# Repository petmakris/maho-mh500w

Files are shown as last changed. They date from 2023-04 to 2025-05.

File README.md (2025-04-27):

# Maho MH500w CNC

Documentation and notes for a Maho MH500W CNC

## Selecting Heidenhain EXE (converters for 

LS-403C has a grating period of 20μm ==> 1 μm resolution in 5 fold interpolation

# Linux CNC Installation

# Software Installation

Start of `bookworm/sid` (use xfce):

https://cdimage.debian.org/cdimage/unofficial/non-free/cd-including-firmware/

- Remove cdrom from sources: sudo nano /etc/sources.list
- `sudo apt install ethtool`

Check driver alignment:

- `lspci`
- `sudo ethtool -i enp2s0`

## Install Rods' custom kernel

6.1 exists in my NAS

- install headers
- install kernel
- `sudo apt install grub-customizer`
- `sudo apt install r8168-dkms`

# Mesa 7i97

## Network interface:

`sudo vim /etc/network/interfaces`

```
auto enp2s0
iface enp2s0 inet static
address 10.10.10.1 or 192.168.1.1
```
Restart network: `sudo systemctl restart networking`

`mesaflash --device 7i97 --addr 10.10.10.10 --readhmid`

# ??? sudo ethtool -C eth0 rx-usecs 0

# LinuxCNC

`sudo apt install linuxcnc-uspace linuxcnc-uspace-dev mesaflash`

Let it run for a while. While it is running,
in another window, check the network latency by reviewing the TMAX settings on your card

`halcmd show param hm2*tmax*`

```
Parameters:
Owner   Type  Dir         Value  Name
     7  s32   RW              0  hm2_7i97.0.read-request.tmax
     7  bit   RO          FALSE  hm2_7i97.0.read-request.tmax-increased
     7  s32   RW         704022  hm2_7i97.0.read.tmax
     7  bit   RO          FALSE  hm2_7i97.0.read.tmax-increased
     7  s32   RW          42126  hm2_7i97.0.write.tmax
     7  bit   RO          FALSE  hm2_7i97.0.write.tmax-increased
```

# Notes

[Enable outputs](https://forum.linuxcnc.org/27-driver-boards/46253-mesa-7i97-analog-out-issue#246257)

# Notes

- MAHO Original color: RAL6011

## Pull Stud

- SK40 ISO 7388 II B
  - The short pull stud for SK
  - The long for BT 



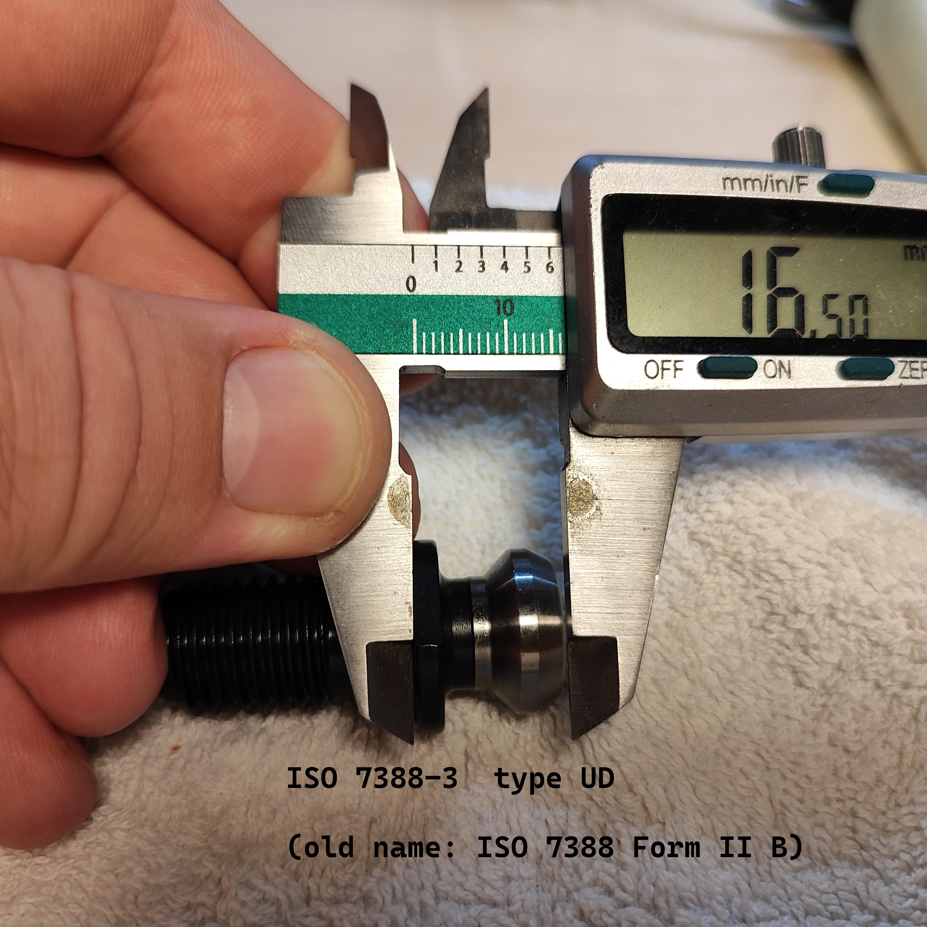
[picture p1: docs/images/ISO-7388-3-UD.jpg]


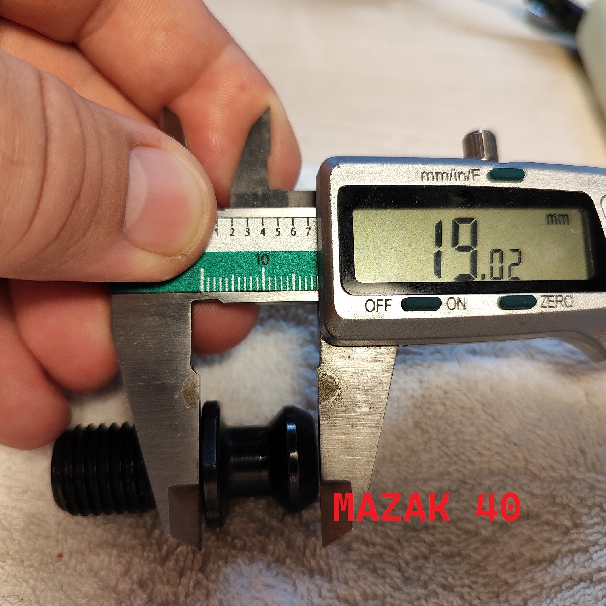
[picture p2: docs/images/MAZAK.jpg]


ISO Standard: https://www.iso.org/standard/68845.html

What fits to a CAT40 cone:
    Pull studs ISO 7388-3 Form UD | M16 | former norm ISO 7388 Form II B (https://bit.ly/38K9Pz4)
    Kemmler
        Order number: 404.20.16
        https://www.kemmler-shop.de/en/pull-studs/pull-studs-iso-7388/1509/pull-studs-iso-7388-3-form-ud-m16-with-drill-through-without-o-ring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

What fits to a BT40 cone:
    Longer by 3mm.
    Kemmler:
        Order number: 404.20.16.20
        https://www.kemmler-shop.de/en/pull-studs/pull-studs-iso-7388/1511/pull-studs-iso-7388-3-form-ud-m16-with-drill-through-incl.-o-ring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

# Gallery









received (1)

received (6)

received (7)

received (9)

received (50)

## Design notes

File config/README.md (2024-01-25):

# Limits

LJ12A3-4-Z/EX - Output Type: NPN NO (Normal Open)

```
Axis    Desc        Cable       Exten.      Name        MESA 7i97
----------------------------------------------------------------------
        Vcc         Brown       Brown       lim-x-pwr   24V
Χ       Signal      Black       White       lim-x-out   TB4-pin4-IN2
        Ground      Blue        Green       lim-x-com   TB4-pin6-COMMON-2,3

        Vcc         Brown       Brown       lim-y-pwr   24V
Y       Signal      Black       White       lim-y-out   TB4-pin5-IN3
        Ground      Blue        Green       lim-y-com   TB4-pin6-COMMON-2,3

        Vcc         Brown       Brown       lim-z-pwr   24V 
Z       Signal      Black       White       lim-z-out   TB4-pin7-IN4
        Ground      Blue        Green       lim-z-com   TB4-pin9-COMMON-4,5
```

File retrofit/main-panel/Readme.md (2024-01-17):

# Requirements

Out of 32 inputs use

- Use a potentiometer for jogging      POT2218PS2-10K 
- Use a potentiometer for Feed Over    POT2218PS2-10K 
- Use a potentiometer for Spindle      POT2218PS2-10K 

- 4 for analog
- 6 for pendant
- 18 for generic buttons

==> Out of 16 output, 12 to be used by LEDs

LED green   6x TME 19010351
LED red     6x TME 19010353

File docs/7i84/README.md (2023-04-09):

The Smart Serial Card Configuration is very new.

At this time the Smart Serial Card will create
a net with a signal name and you will have to 
add the input or output pin name or create simple 
I/O connections.

The 7i83 and 7i87 are not currently supported.

The Smart Serial Card configuration will not load
from the ini file at this time.

## SSERIAL Wiring using a standard CAT5 Cable:

Pin 0 is at the bottom

TB2 PIN	    SIGNAL      CAT5 PIN	CAT5 568B COLOR
--------------------------------------------------------
15	        GND	        4,5	        BLUE, BLUE / WHITE
16	        RX+	        6	        GREEN
17	        RX-	        3	        GREEN / WHITE
18	        TX+	        2	        ORANGE
19	        TX-	        1	        ORANGE / WHITE
20	        +5V	        7,8	        BROWN / WHITE,BROWN

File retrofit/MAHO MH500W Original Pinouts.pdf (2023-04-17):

19X7 | Inputs | Color
19X7-1 | Handwheel X | ws | white | 278
19X7-2 | Handwheel Y | br | brown | 279
19X7-3 | Handwheel Z | gn | green | 280
19X7-4 | 24V (αυτο ειναι ένδειξη) | ge | yellow | 200
19X7-5 | Spindle OFF | gr | gray | 211
19X7-6 | / (Spindle Feed Stop) | rs | orange | 212
19X7-7 | Lubricant Pump Feedback | bl | blue | 213
19X7-8 | No Function | rt | red
19X7-34 | | sw | black
19X6 | Outputs | Color | | | Relay
19X6-1 | X Axis Handwheel Clutch | ws | white | 28A1-3 | 28A1-K2
19X6-2 | Y Axis Handwheel Clutch | br | brown | 28A1-4 | 28A1-K3
19X6-3 | Z Axis Handwheel Clutch | gn | green | 28A1-5 | 28A1-K4
19X6-4 | Spindle CW | ge | yellow | 28A1-14 | 28A1-K6
19X6-5 | Spindle CCW | gr | gray | 28A1-28 | 28A1-K7
19X6-6 | Coolant Pump | rs | orange | 28A1-29 | 28A1-K8
19X6-7 | Tool Release | bl | blue | 28A1-30 | 28A1-K9
19X6-8 | Central Lubrication | rt | red | 313 | 4V1 / 4K1
19X6-9 | No Function
19X6-34 | / ESTOP | sw | black | 28A1-2 | 28A1-K1
19X4 | Setpoint | Color
19X4-1 | X Axis | br | brown | E101
19X4-2 | X Axis | bl | blue | E102
19X4-3 | Y Axis | ws | white | E201
19X4-4 | Y Axis | gr | green | E202
19X4-5 | Z Axis | ge | yellow | E301
19X4-6
19X4-7
19X4-8
19X4-9 | Z Axis | rs | rs | E302
28A1 | Relay Board
K1 | Emergency Stop Switch
K2 | X Axis Handwheel Clutch
K3 | Y Axis Handwheel Clutch
K4 | Z Axis Handwheel Clutch
K5
K6 | Main Drive Anti-Clockwise
K7 | Main Drive Left Rotation
K8 | Release Tool Clump
K9 | Lubricant Pump
K10

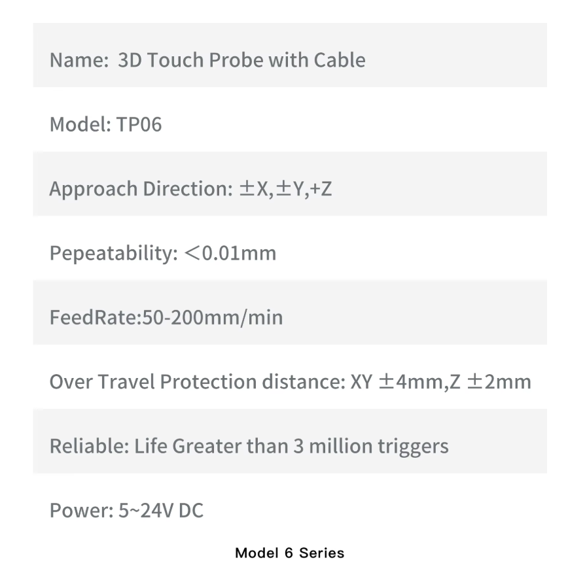
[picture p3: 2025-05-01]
docs/Probe/aliexpress-probe/specs.png

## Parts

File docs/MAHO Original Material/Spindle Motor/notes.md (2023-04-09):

ABGA-090LB-04A 

Page 90 in PDF (Brake morots, Series ABGA)

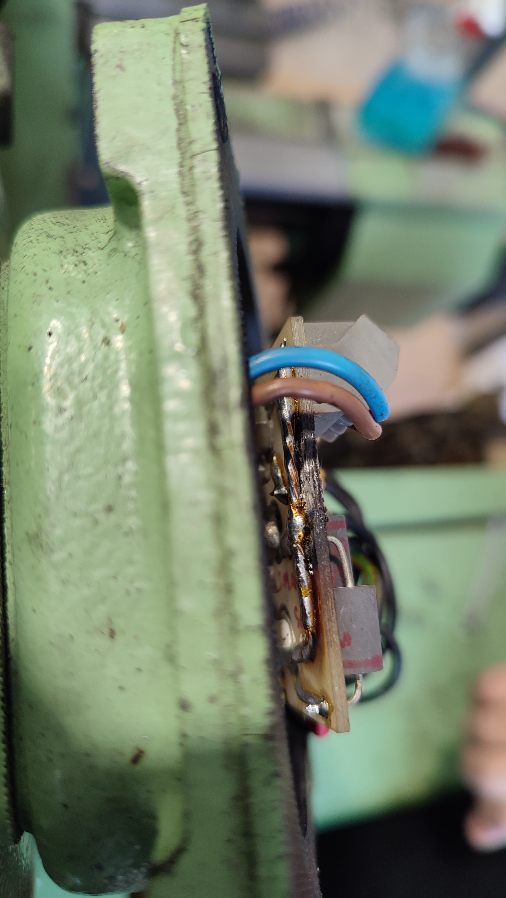
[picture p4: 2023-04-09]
docs/MAHO Original Material/Spindle Motor/gallery/junction-7.jpg

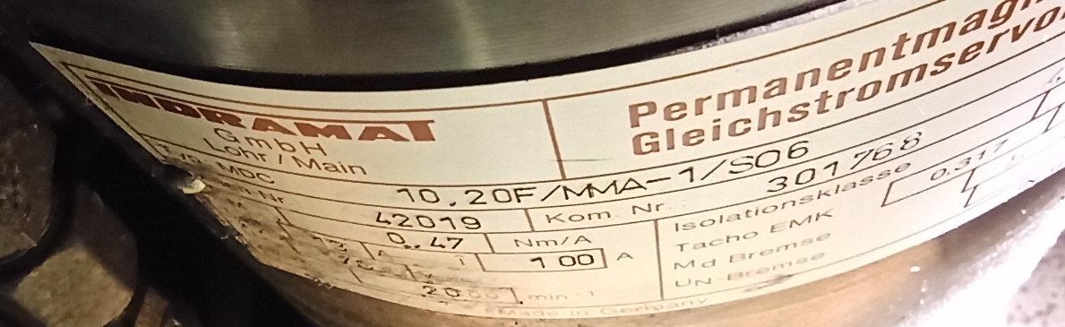
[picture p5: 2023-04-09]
docs/MAHO Original Material/INDRAMAT/Z-AXIS 10.20F ΜΜΑ-1 S06/Motor-Z-4.jpg

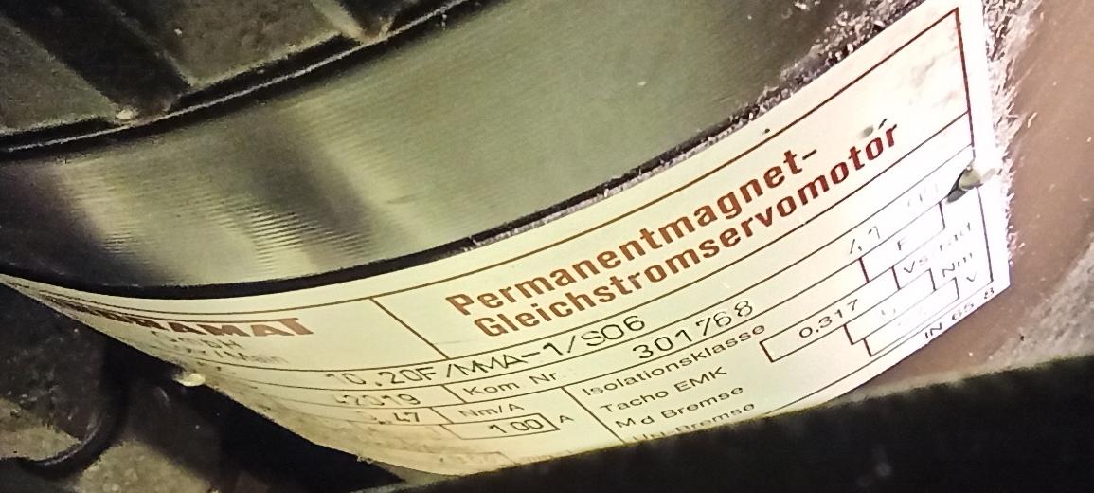
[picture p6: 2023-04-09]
docs/MAHO Original Material/INDRAMAT/Z-AXIS 10.20F ΜΜΑ-1 S06/Motor-Z-1.jpg

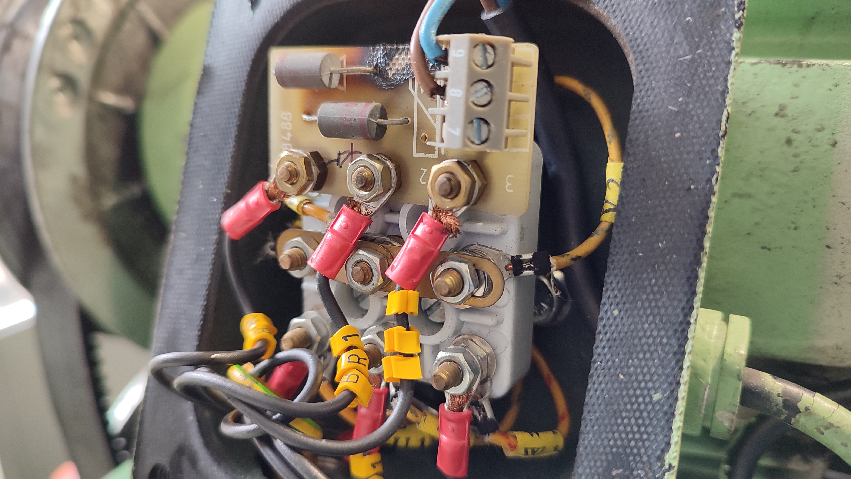
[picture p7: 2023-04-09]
docs/MAHO Original Material/Spindle Motor/gallery/junction-4.jpg

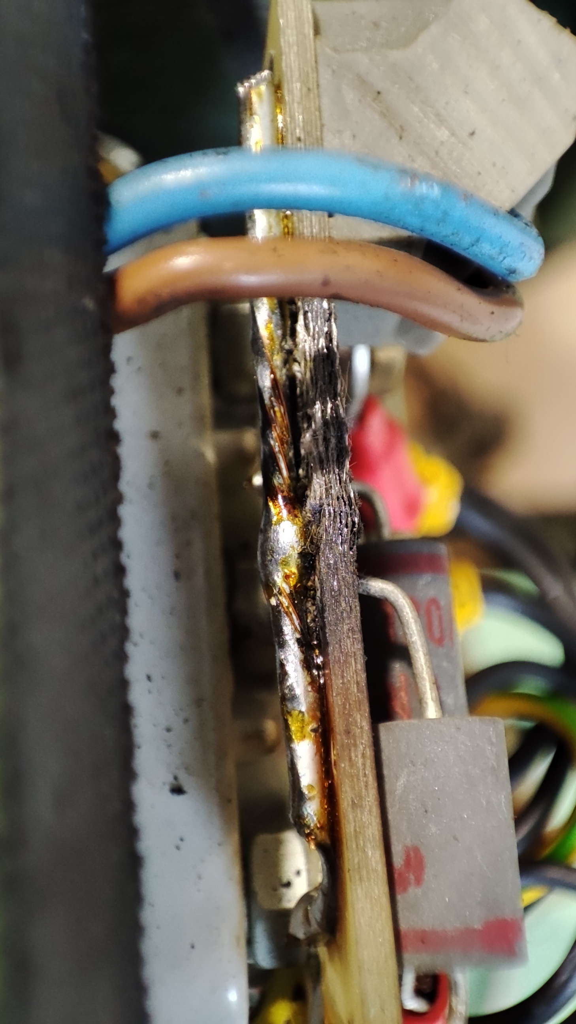
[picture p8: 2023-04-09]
docs/MAHO Original Material/Spindle Motor/gallery/junction-8.jpg

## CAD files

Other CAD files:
docs/7i97/7i97-footprint.3dm
retrofit/main-panel/panel.3dm

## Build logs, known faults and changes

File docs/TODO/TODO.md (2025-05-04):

# Spindle Encoder

- [ ] GND (currently Yellow -> Blue on proximity)
- [ ] 5V to 24V (currently Brown-> Brown on proximity) (5V from enc connector)
- [ ] SPINDLE_ENCODER (currently Pink -> Black on proximity) [LinuxCNC Input]

# MIST

Each relay has a 200 mA current rating.

- [ ] GND
- [ ] 24V
- [ ] RELAY_1 (Level 1 Mist) [LinuxCNC Output]
- [ ] RELAY_2 (Level 2 Mist) [LinuxCNC Output]
- [ ] RELAY_3 (Air Blow) [LinuxCNC Output]

# Probe

- GND
- [ ] 5V to 24V (I need 5V, I can take 5V from mesa)
- [ ] PROBE_SIGNAL  [LinuxCNC Input]

NOTE: I need a quick connector for the probe.

# Tool Change

- [ ] GND
- [ ] 24V
- [ ] TOOL_RELEASE [LinuxCNC Input]

# Machine Jog Buttons

- GND
- [ ] X- [LinuxCNC Input]
- [ ] X+ [LinuxCNC Input]
- [ ] Y- [LinuxCNC Input]
- [ ] Y+ [LinuxCNC Input]
- [ ] Z- [LinuxCNC Input]
- [ ] Z+ [LinuxCNC Input]

# Potential cables

https://www.acdcshop.gr/wirejz50016g05mm2unshielded300500vpvccustranded-p-38588.html
https://www.acdcshop.gr/wireunitronic174liyy16x034mm2unshielded500vpvccugrey-p-38479.html

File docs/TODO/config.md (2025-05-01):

# Panel Buttons

- Auto enable teleop mode when pressing Z+, jogging does not work on program stop. 

- Wiring for EasyProbe, JogButtons, Mist

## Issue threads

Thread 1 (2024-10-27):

Questions

NoGare, 2024-10-27:
Good Evening,

I have an opportunity to acquire a MH600W, and in the process of doing my research on whether it's a good fit - I happened across your github repo related to your retrofit. Wondering if you might have time to indulge a couple questions I have.

:: Best as I can tell, it seems like your conversion was a success. There is a thread on the linuxCNC forum; that seems to indicate as such.. However I could not determine if you found a solution for the manual hand wheels?

:: Are you powering the machine off 3PH or rewired it to use it on 1PH?

:: I see no mention of it, however I also didn't see a picture of your machine... Does your machine have the rotary table? If so, how did the integration of the encoder go?

Regards -

petmakris, 2025-01-14:
I apologize @NoGare , I missed your message.

- The conversion was succesful but the machine was quite used, it has some backlash on the ballscrew nuts, especially on the X axis, and I can't minimize as much as I wanted the min-ferror. But still works quite well.

- The manual jogging wheel won't work with LinuxCNC, no support for this to my knowledge.

- I am using the machine on 3PH, I used the power electronics as is (the servo amplifiers and everything) so 3PH is necessary.

- No rotary table. I used converters for the Heidenhein encoders (converted the analog current driver signal to TTL).

What happened, did you get the machine after all?

Here are some pictures

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

H-S-W, 2025-03-11:
Hi Petmakris!

I'm starting a linuxCNC conversion on a MH500W2 with a faulty Philips 432/9. Planning to use all your hard work in order to get it up and running again. I'll be using a Rpi5 and a 7I97T and three EXEs.

My first step has been to wire the mill to the 7I97T, but i have a question about the "Limit"s. In the MAHO documentation the limit switches seems to be connected in series 204-207,

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

did you rewire these or simply used 205,206,207 as limit X,Y,Z?

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

Regards,
Hampus

petmakris, 2025-03-11:
Hi @H-S-W ,

I will have to verify this but  I think that **8S1**, **9S1** and **10S1** are the limit switches part of the machine's automation and I didn't touch them. They just power of the ESTOP chain if reached. I believe the signals LIMIT_X, LIMIT_Y and LIMIT_Z (I can see the typos now, geez) are proximity sensors I used for homing the machine with linux CNC.

petmakris, 2025-03-11:
@H-S-W I was planning to use the reference marks , Ι believe the 2.9.x LinuxCNC homing system might support this, but I installed the proximity sensors to get things going, and it still works like that..

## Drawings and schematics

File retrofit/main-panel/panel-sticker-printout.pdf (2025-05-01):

11 | 10 | 9

8

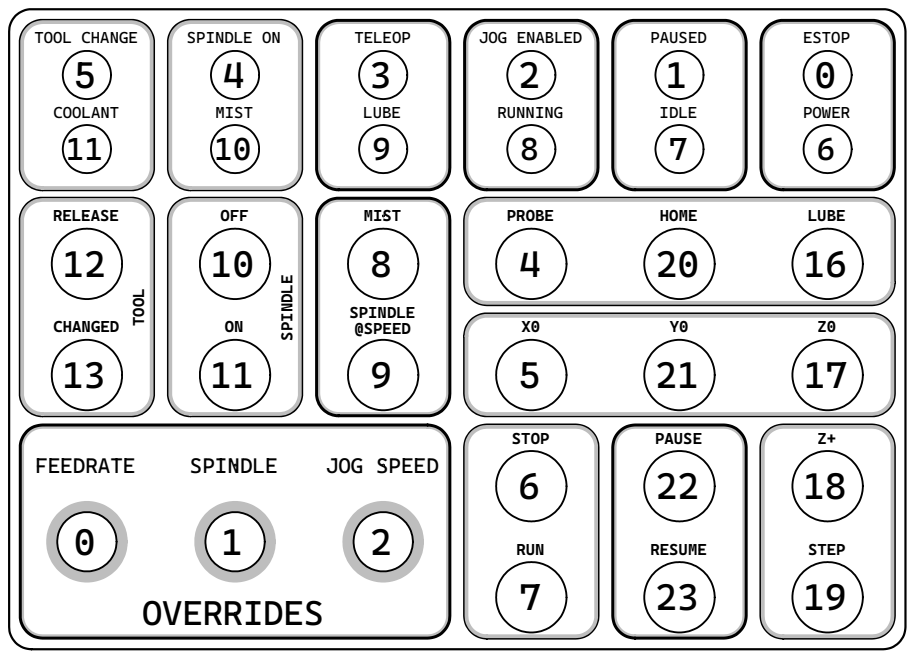
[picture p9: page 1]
CHANGED; X0 SPINDLE; TOOL CHANGE; LUBE; OFF; ESTOP; SPINDLE; @SPEED; PROBE; IDLE; STOP; Z+ PAUSE; OVERRIDES; STEP; FEEDRATE; MIST; JOG SPEED; COOLANT; RUNNING; RELEASE; HOME TOOL; JOG ENABLED; RESUME; SPINDLE ON; TELEOP; RUN; PAUSED; POWER

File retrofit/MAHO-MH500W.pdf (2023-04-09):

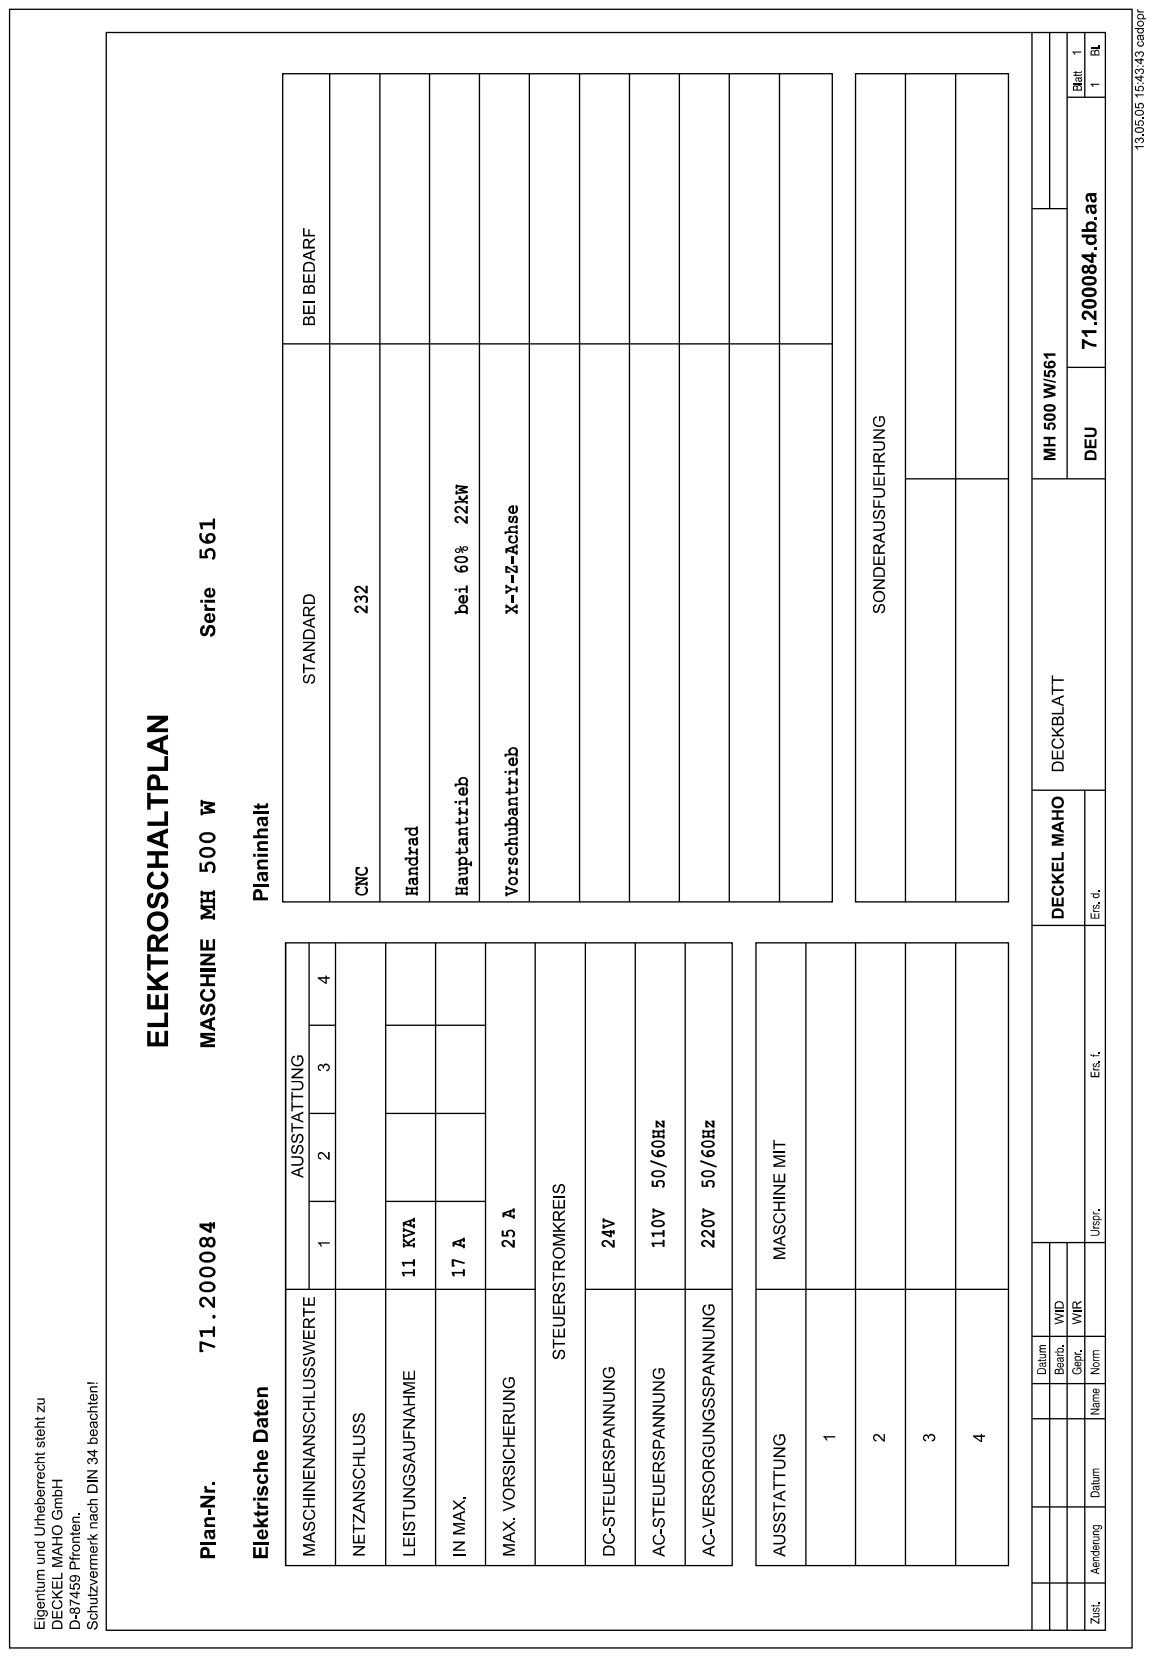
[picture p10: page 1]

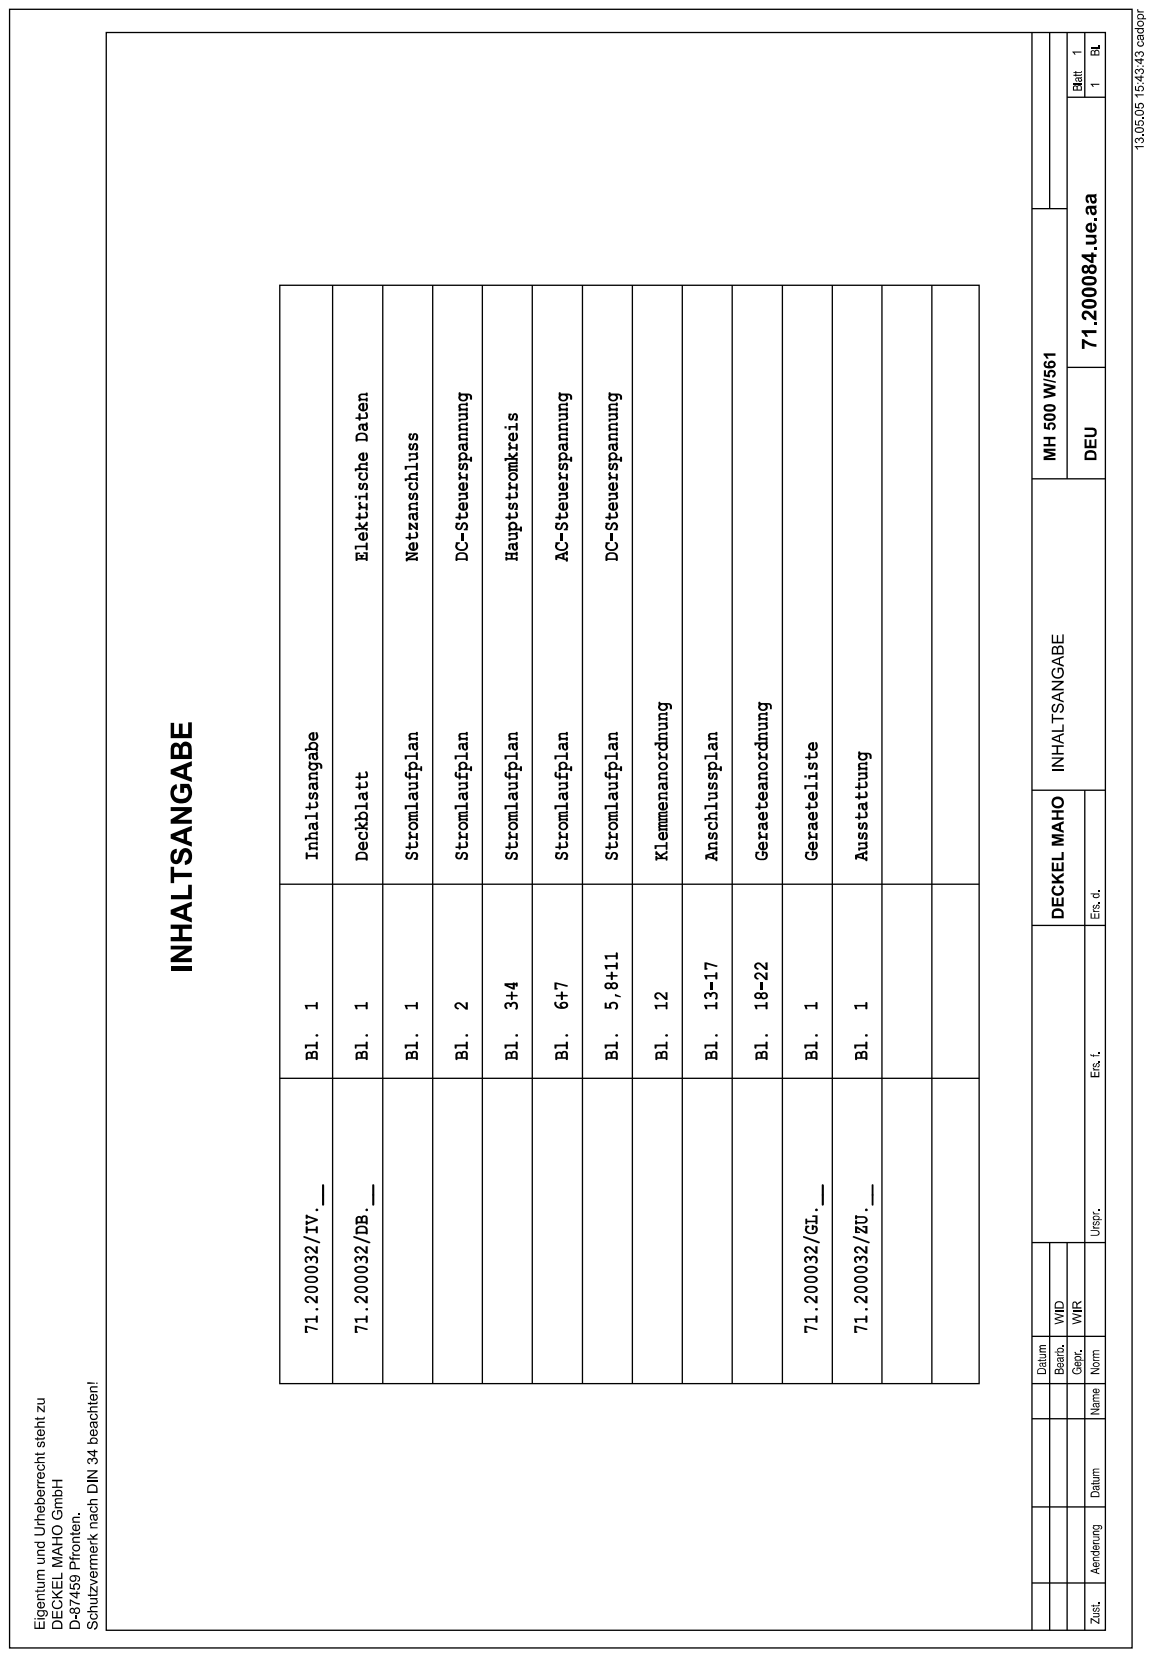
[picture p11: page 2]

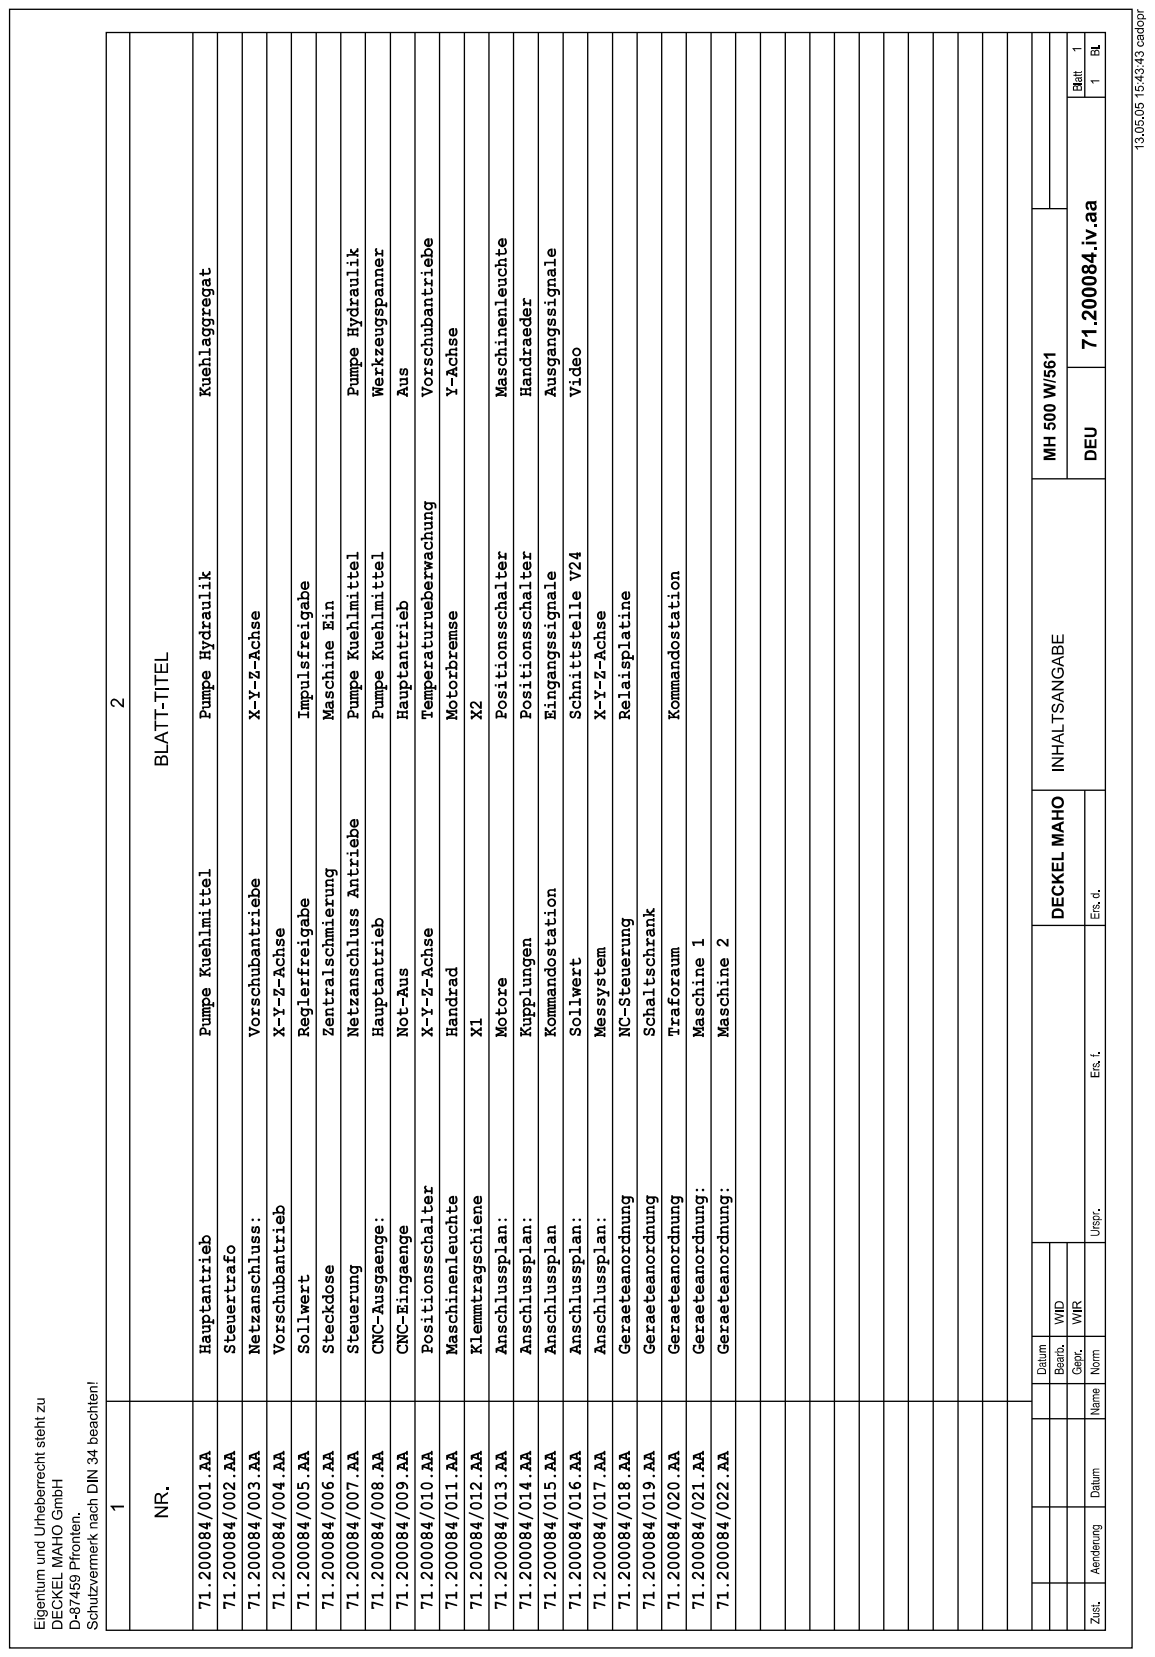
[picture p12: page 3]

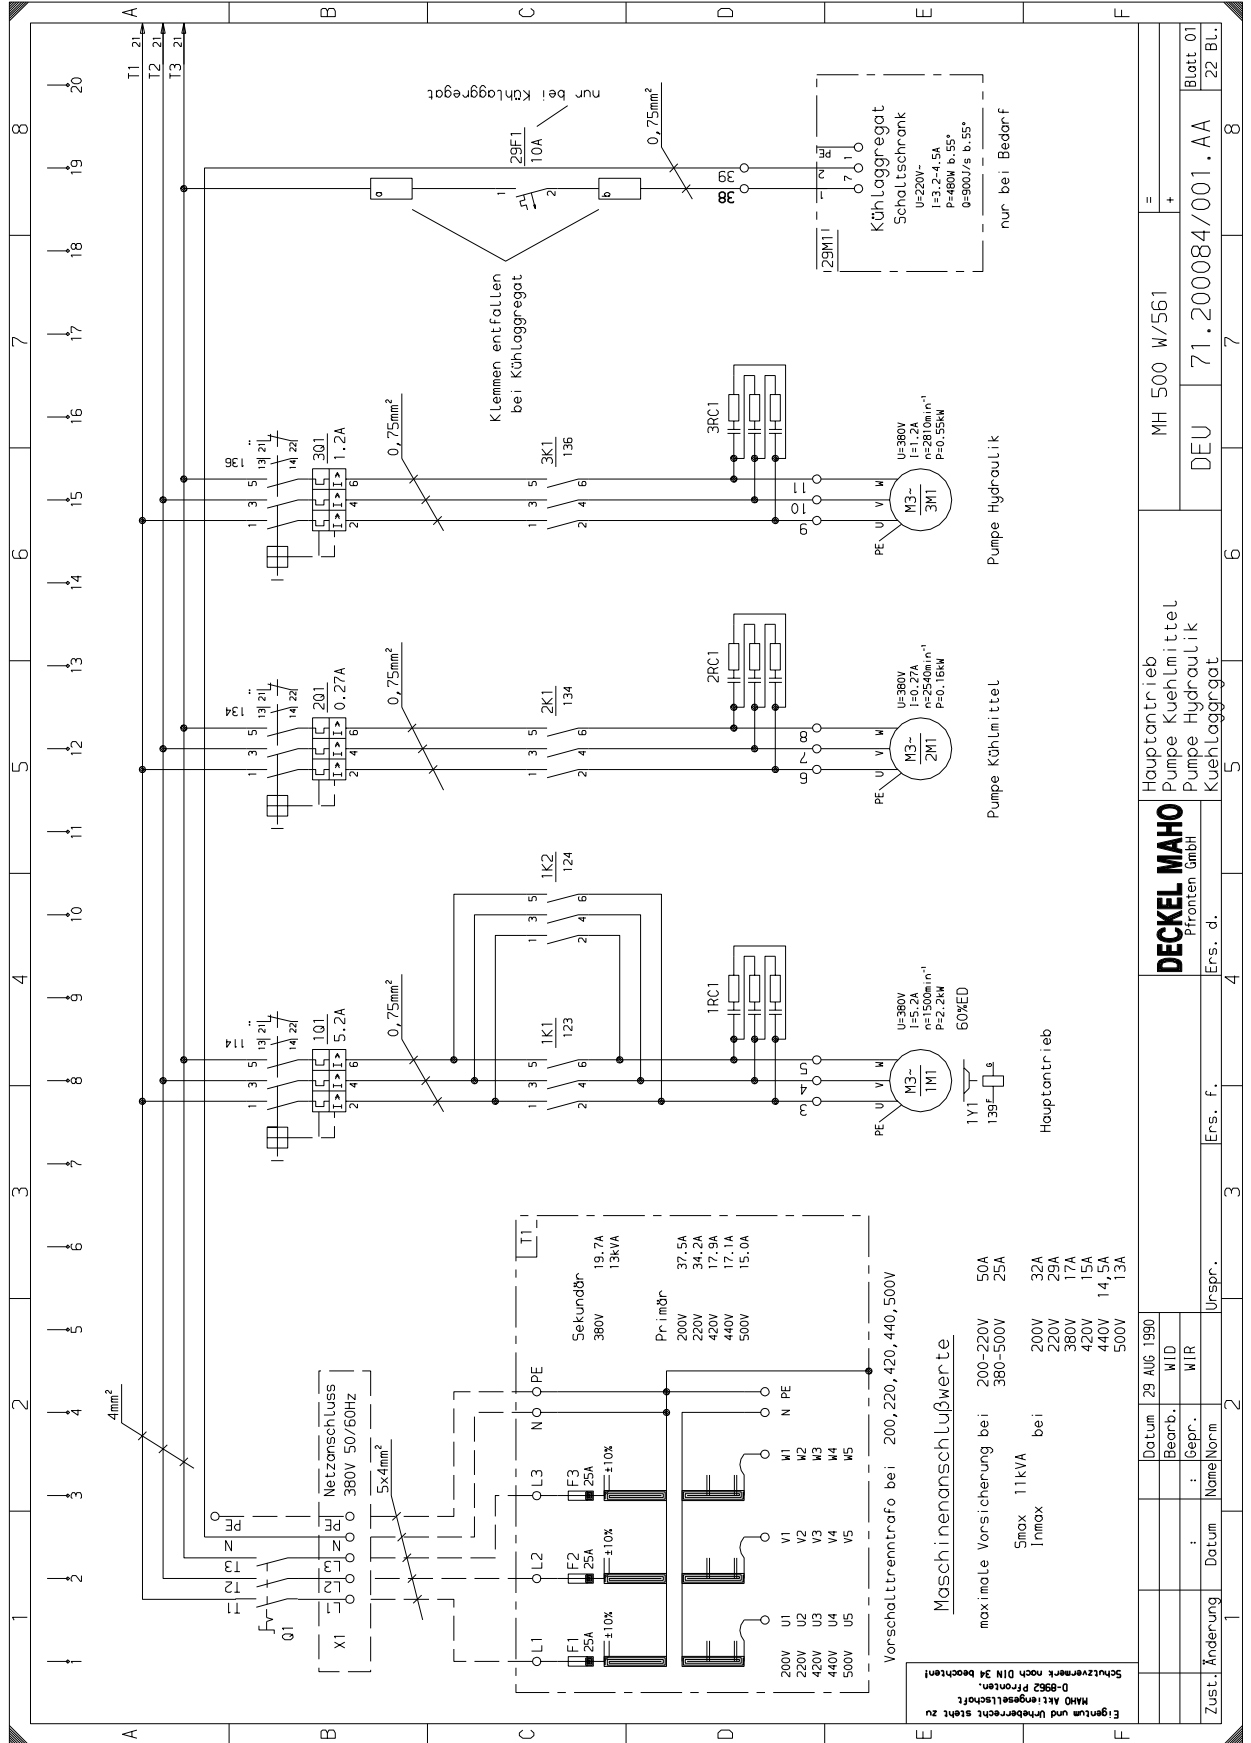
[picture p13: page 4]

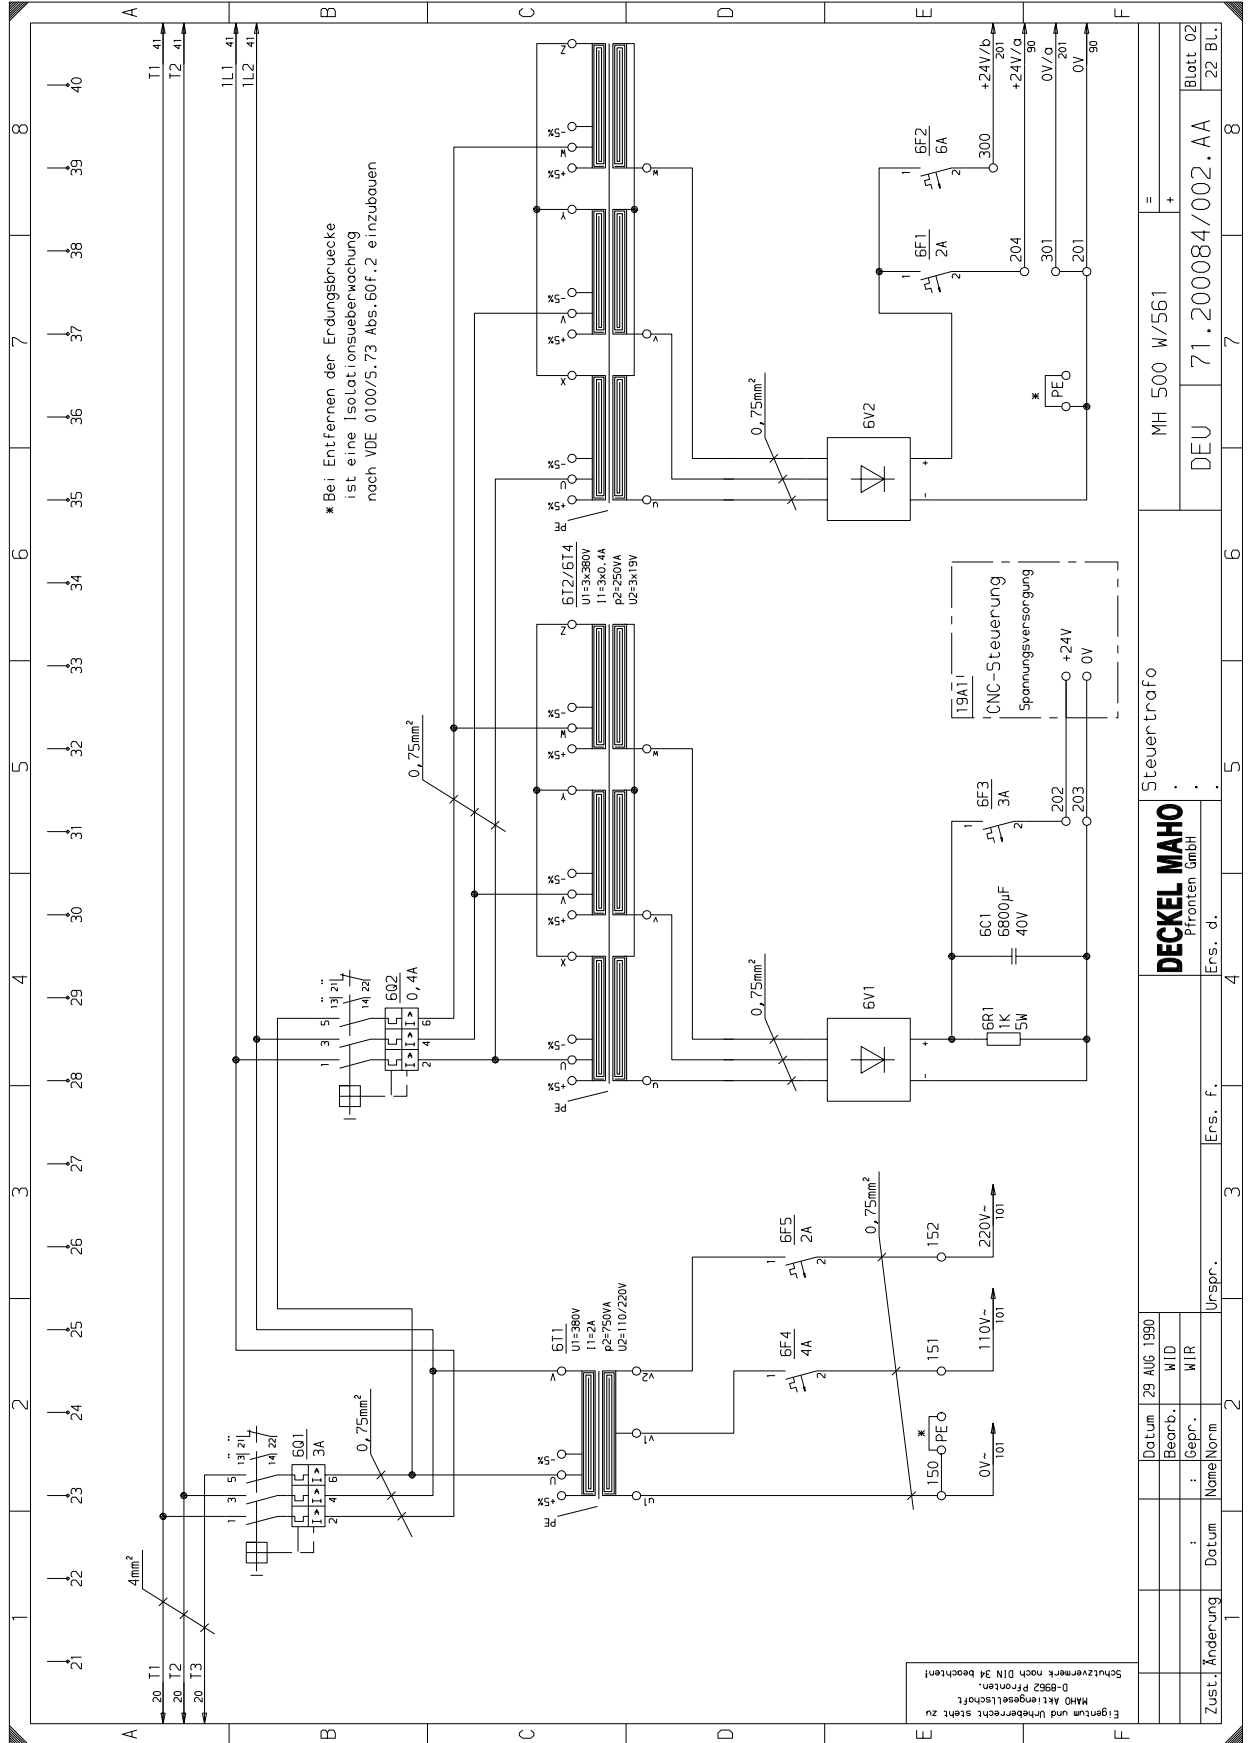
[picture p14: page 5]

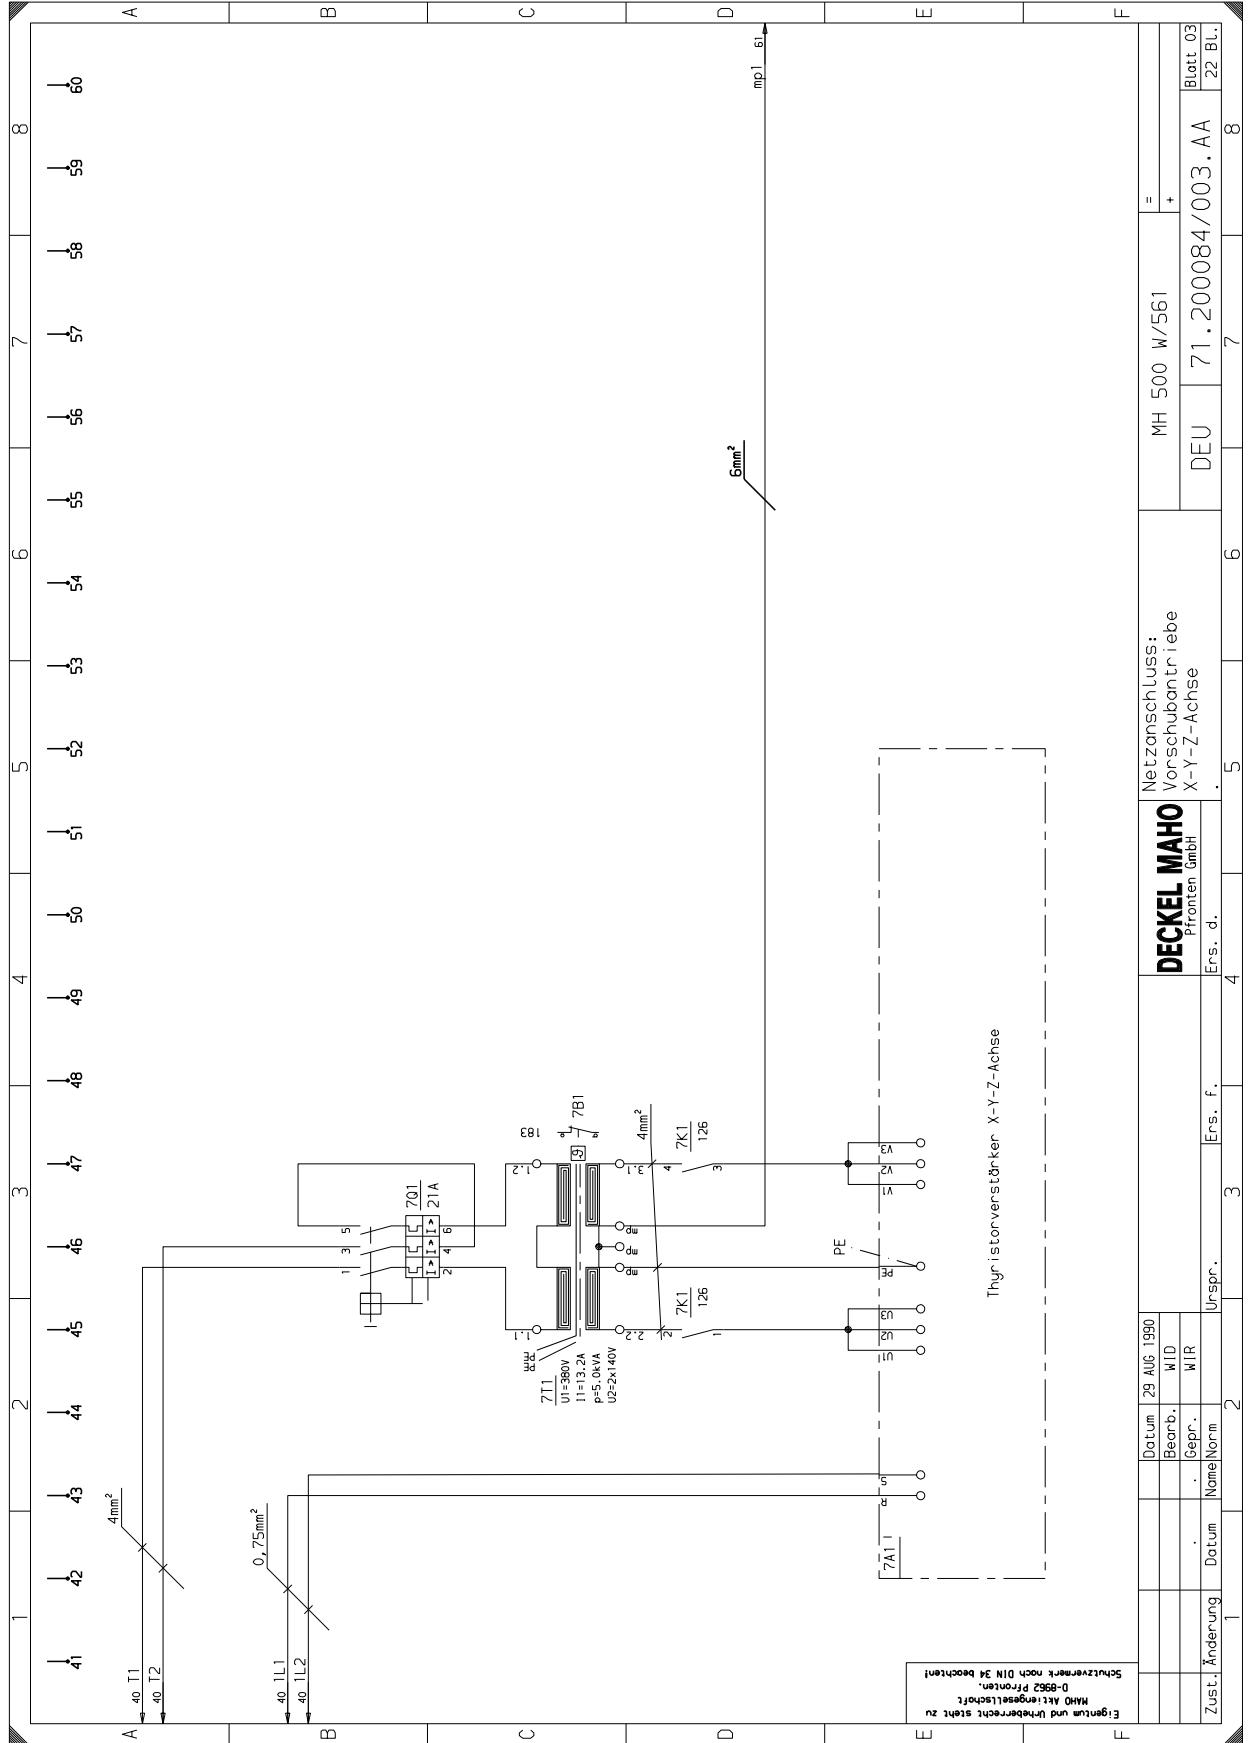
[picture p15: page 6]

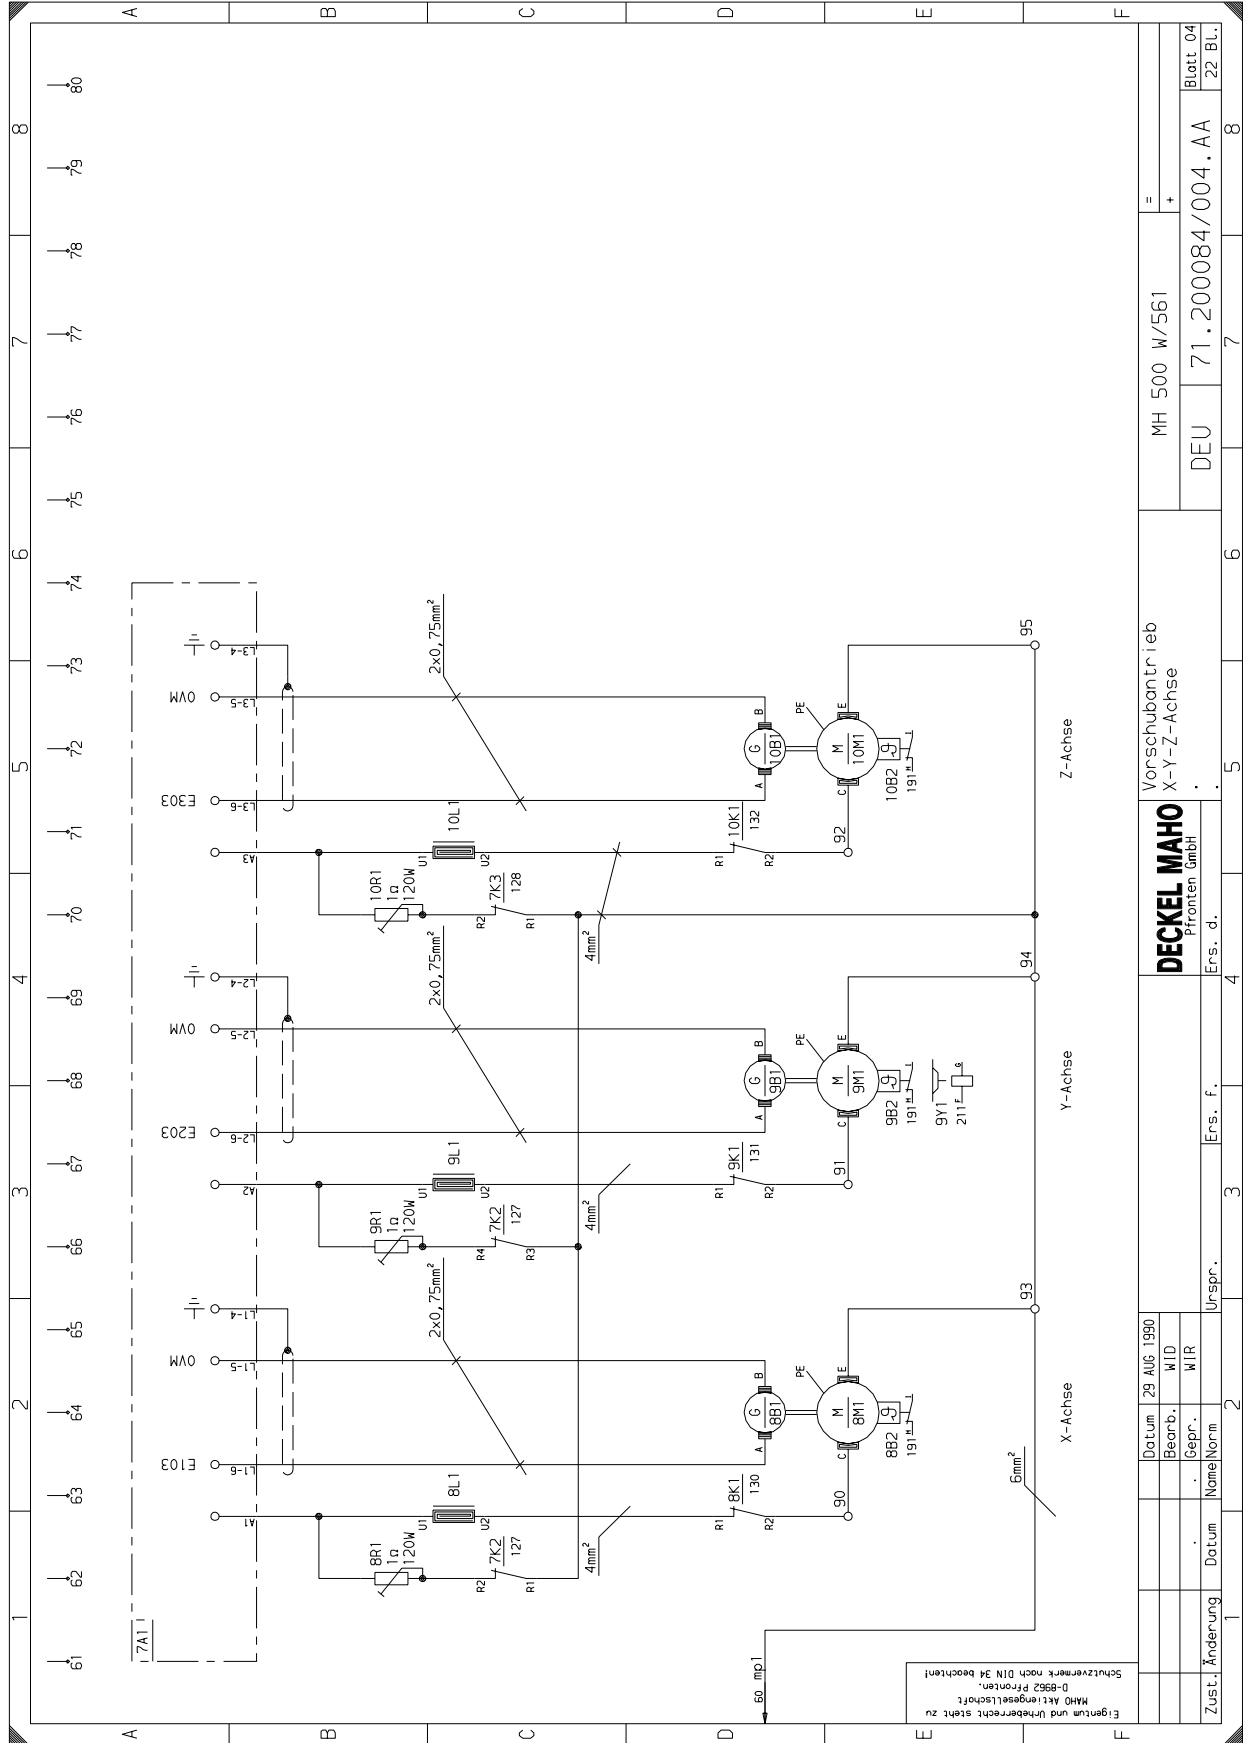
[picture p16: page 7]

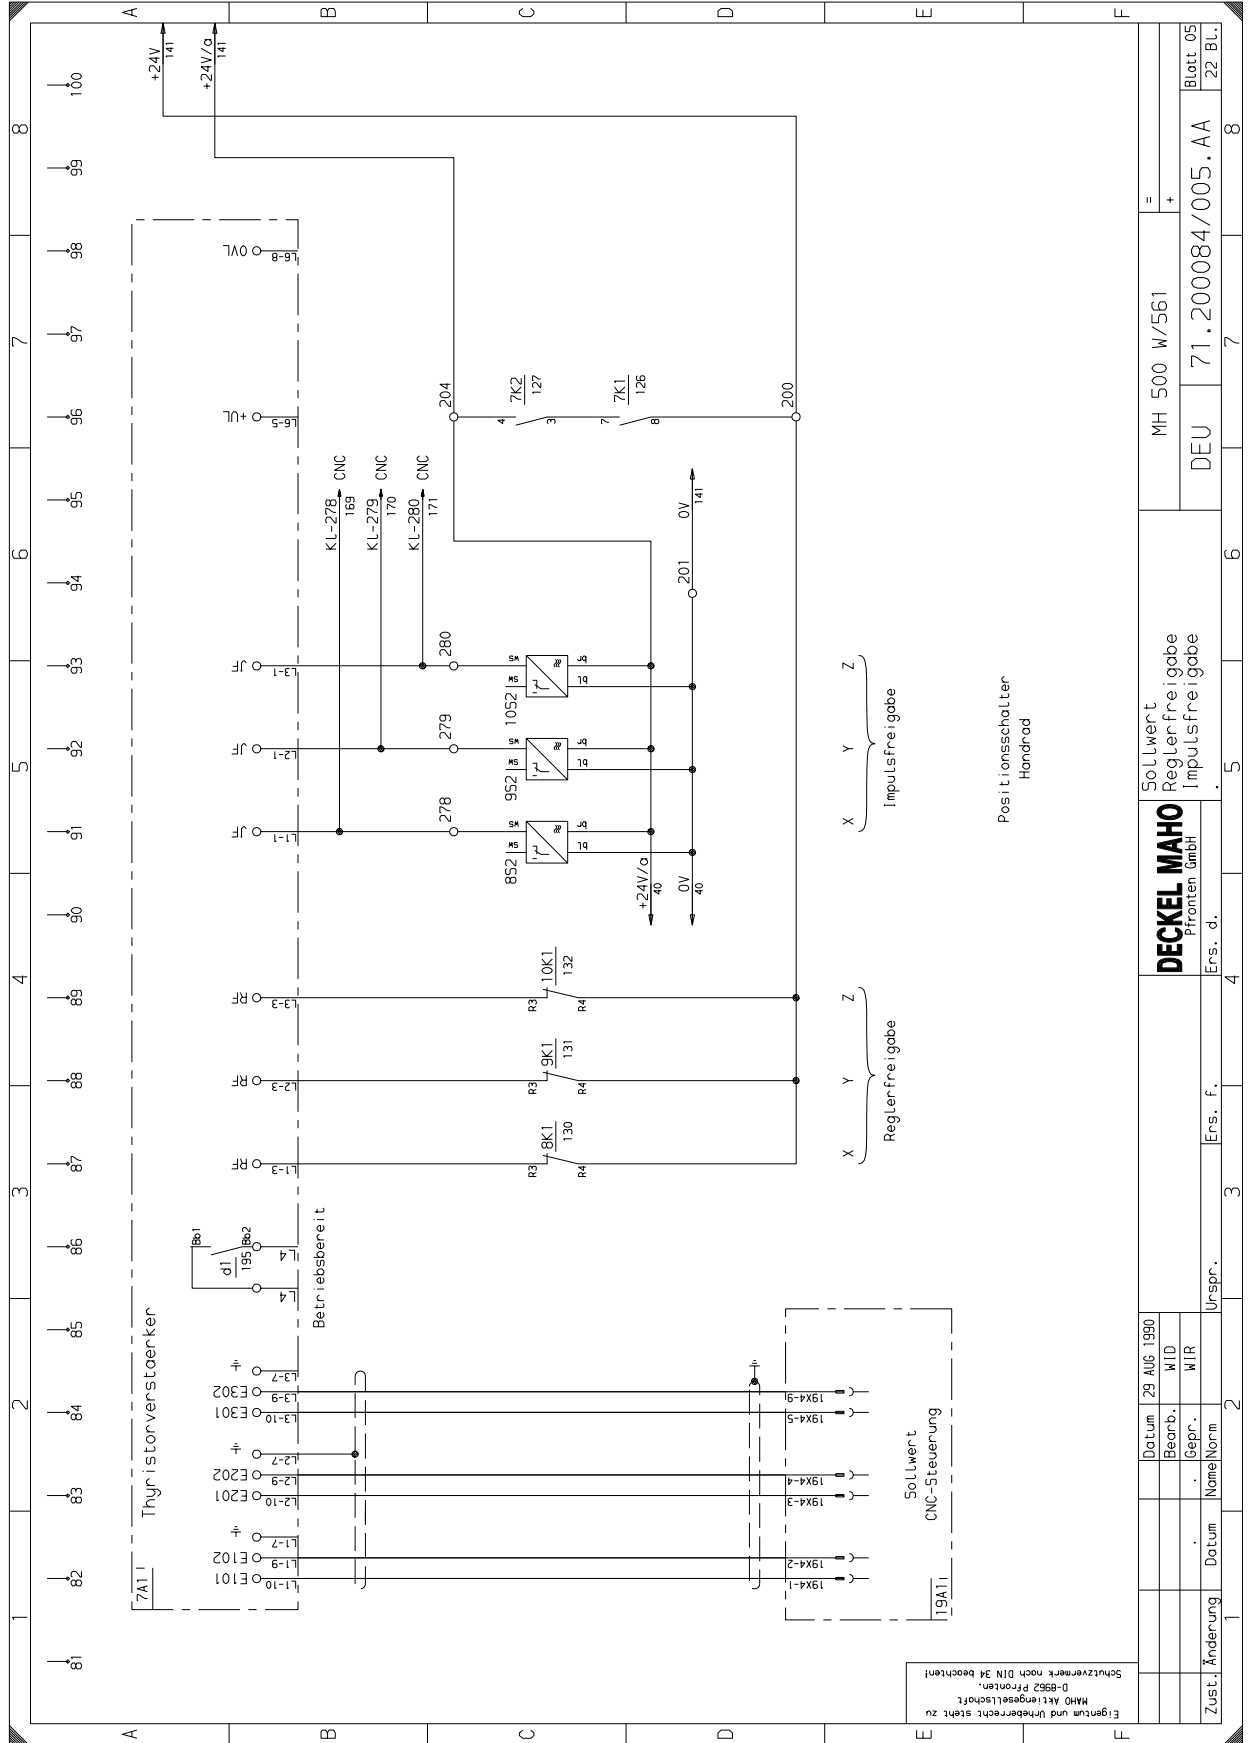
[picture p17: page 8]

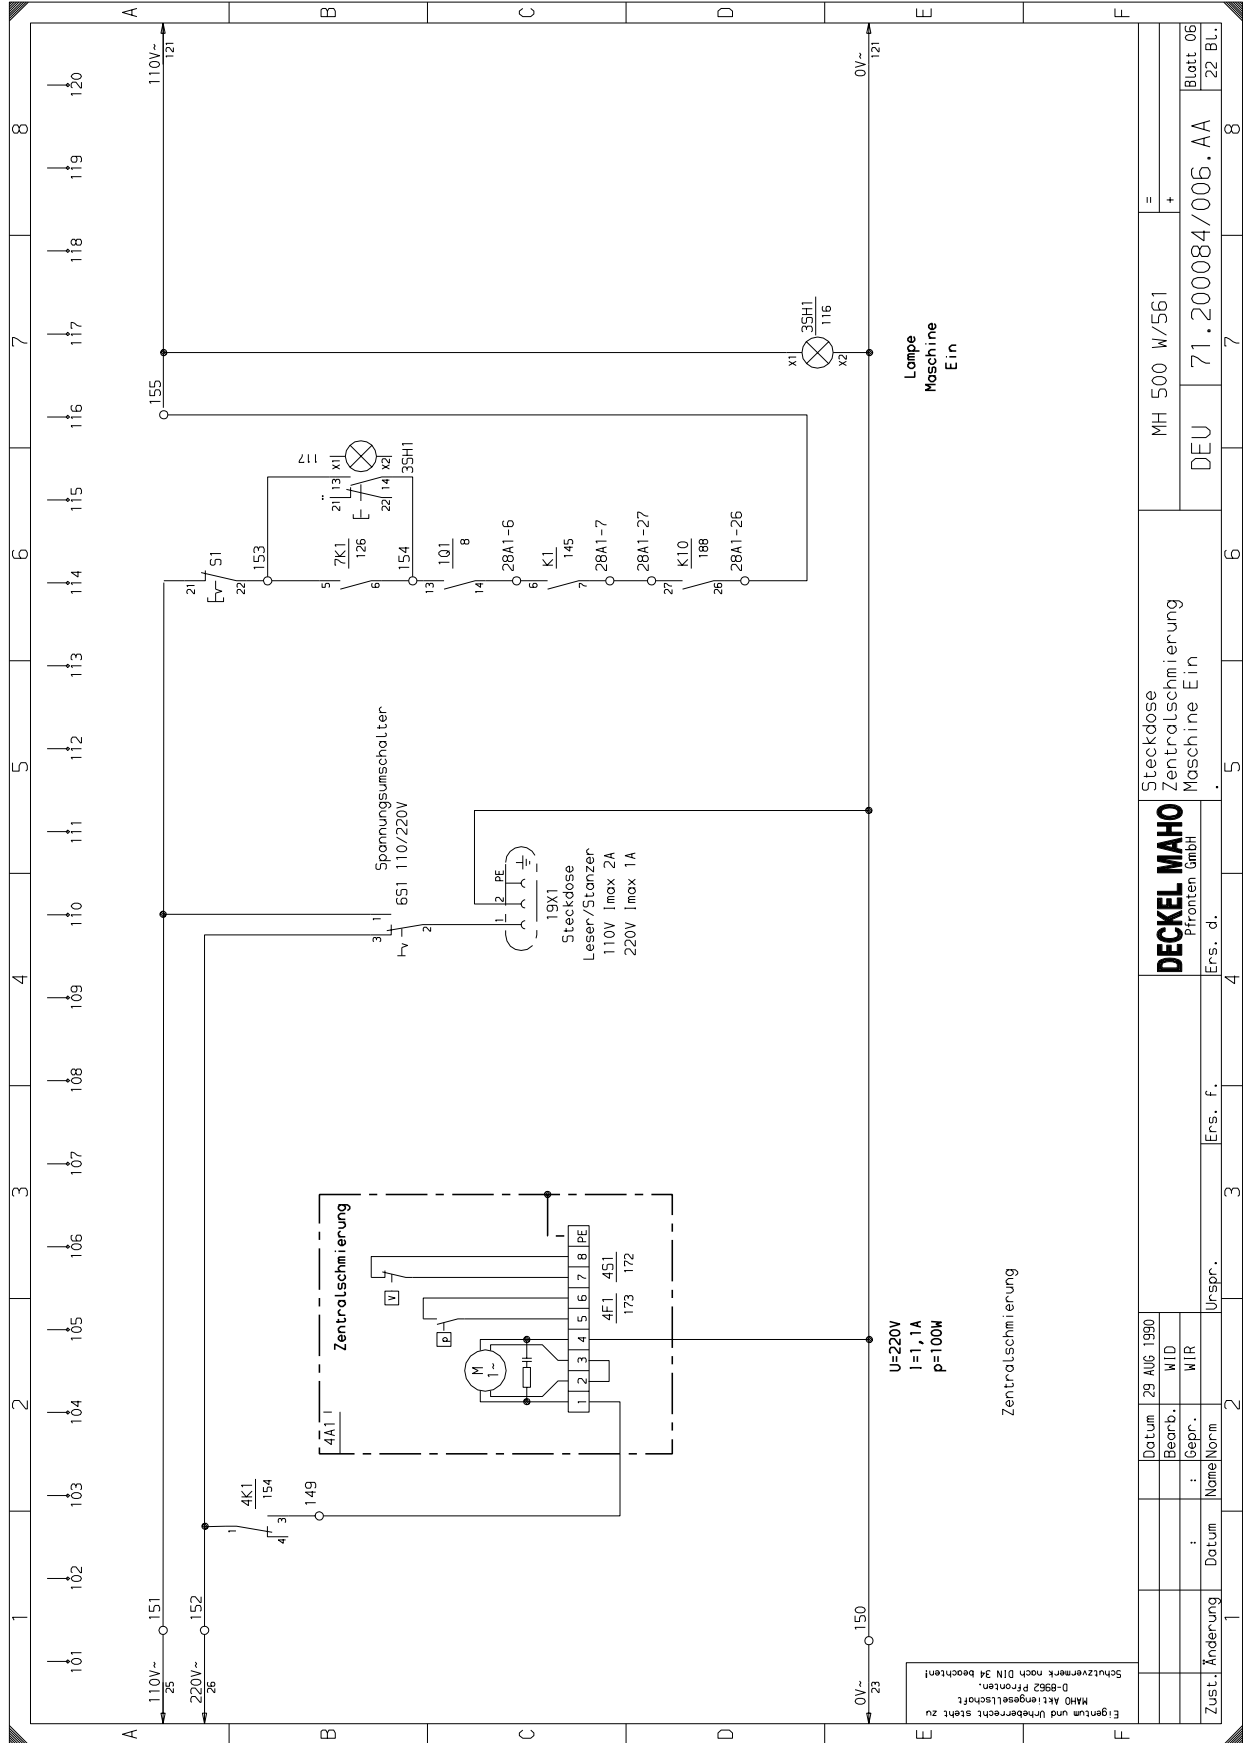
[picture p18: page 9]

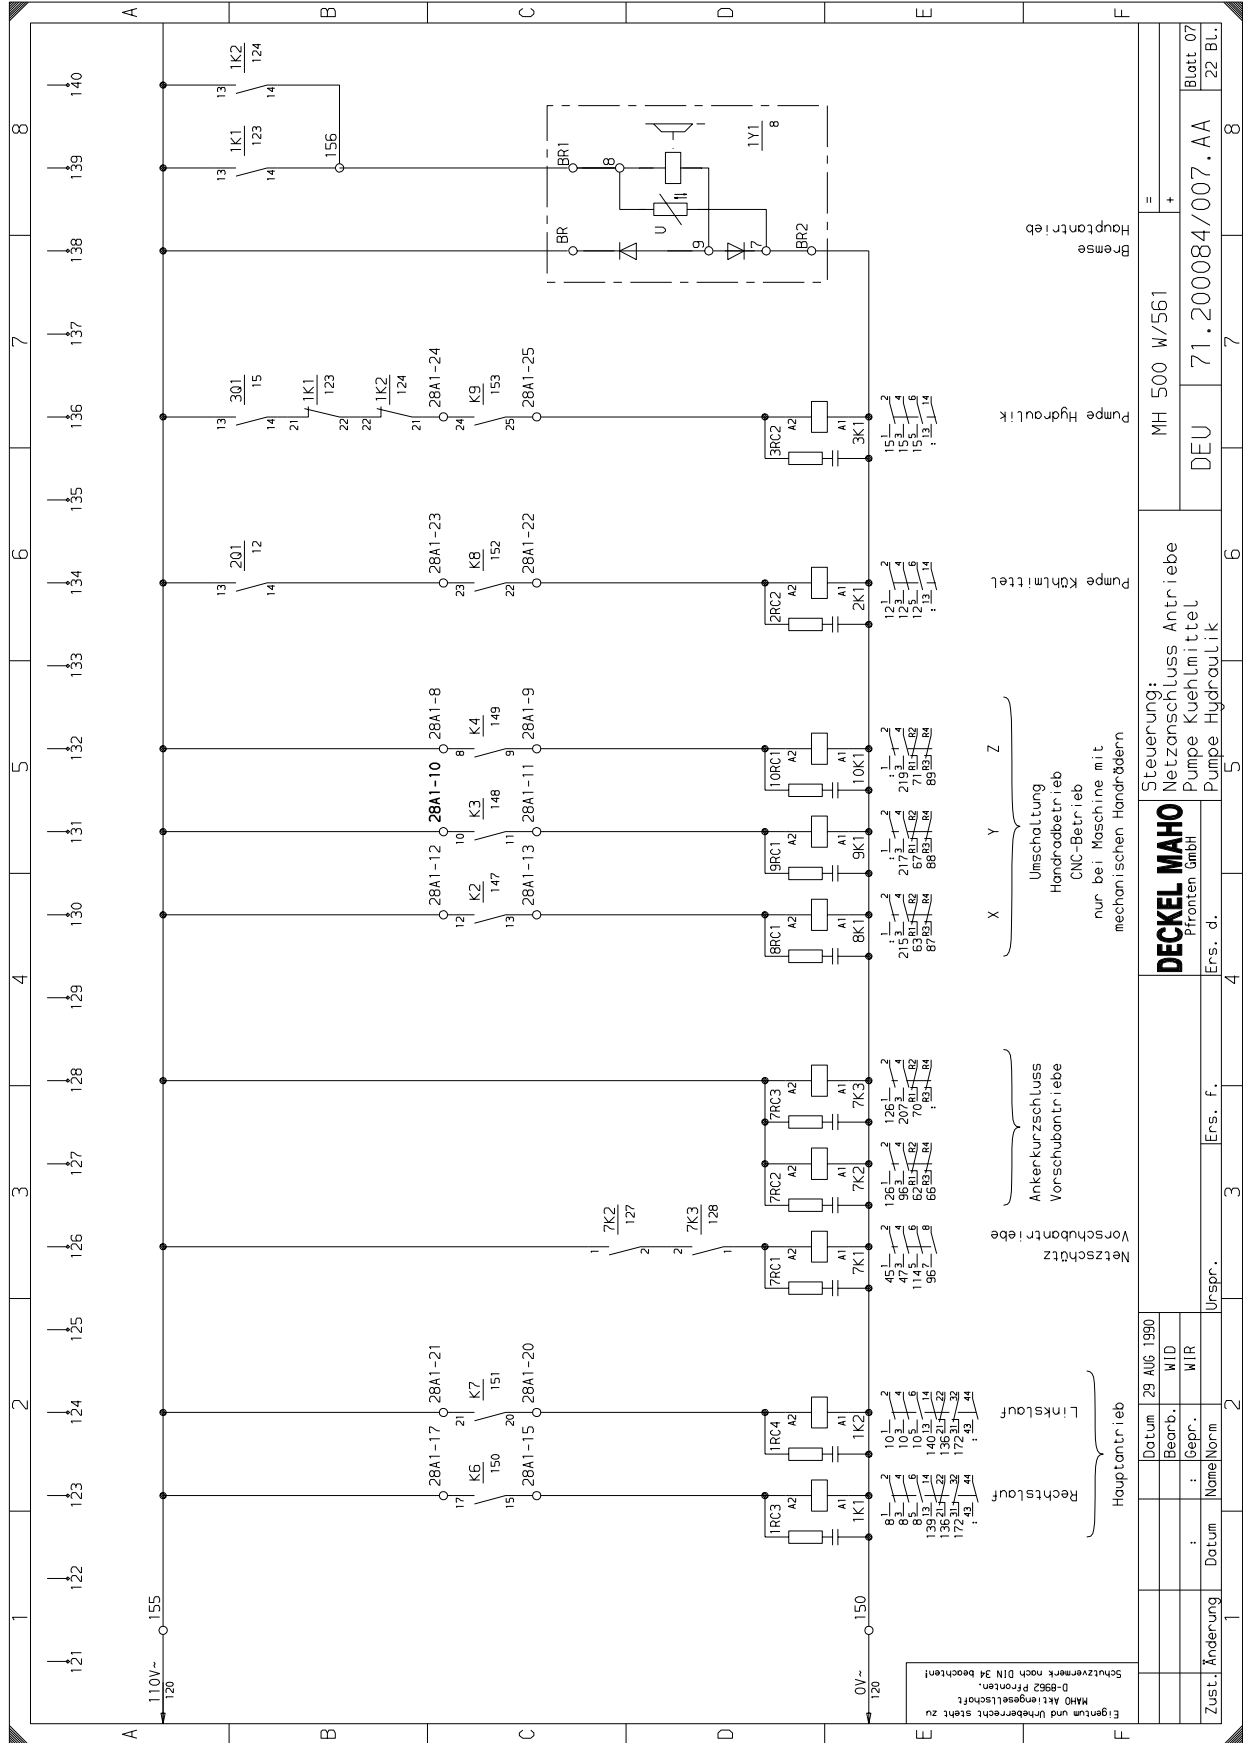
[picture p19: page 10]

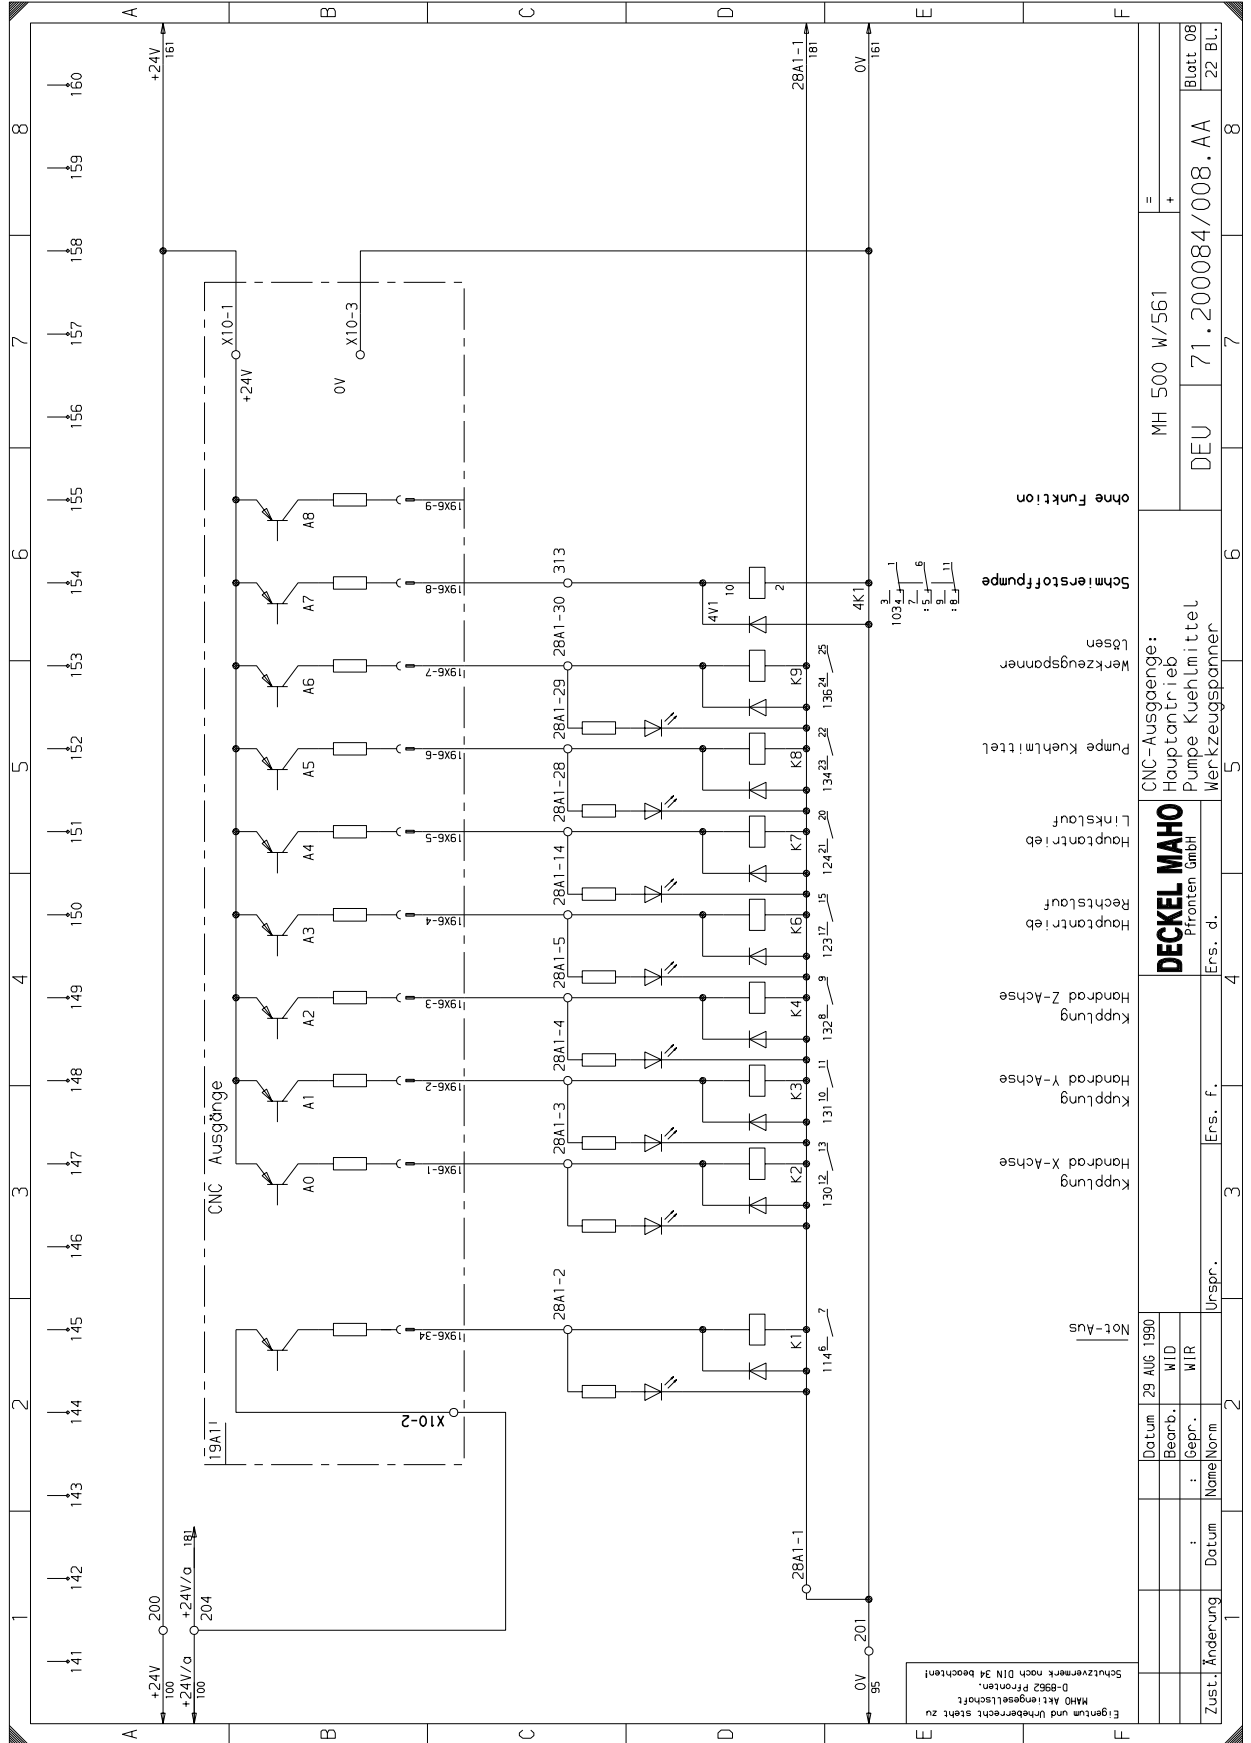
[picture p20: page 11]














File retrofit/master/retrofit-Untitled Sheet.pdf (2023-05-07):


WHITE GRAY WHITE
RED
GRAY WHITE GREEN
BLUE RED GREEN GRAY

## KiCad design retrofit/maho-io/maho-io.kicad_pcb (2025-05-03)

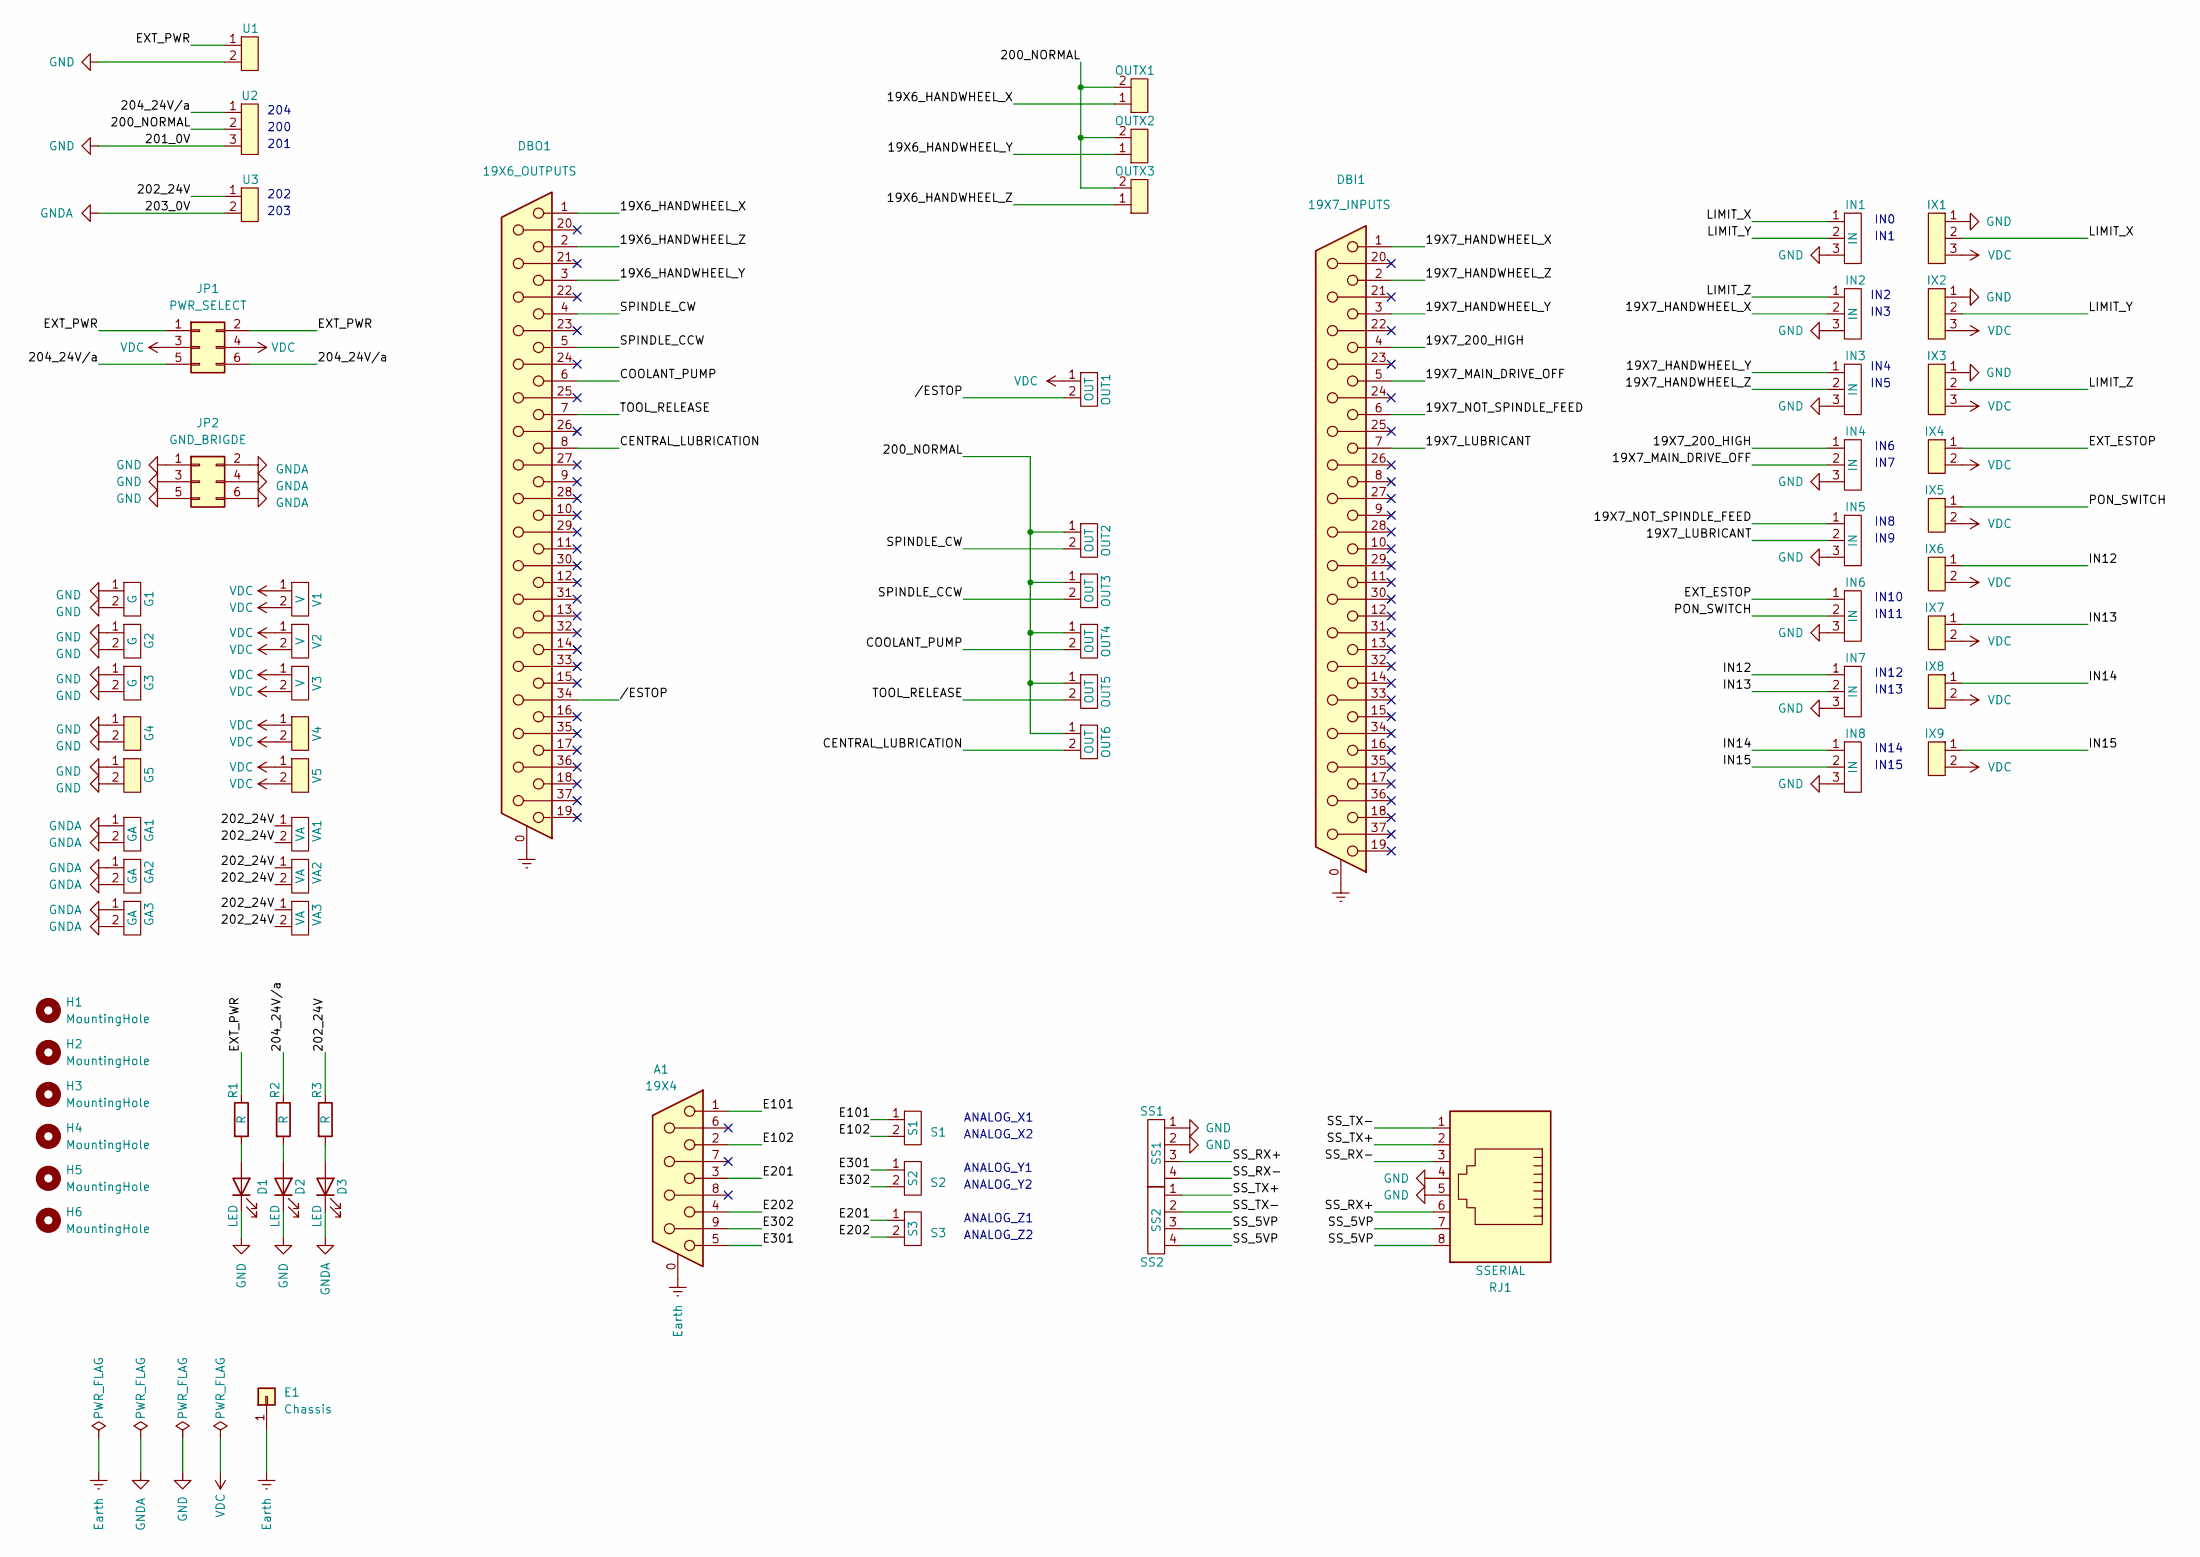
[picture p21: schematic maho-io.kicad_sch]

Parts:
A1: 19X4; DSUB-9_Female_Vertical_P2.77x2.84mm_MountingHoles
D1, D2, D3: LED; LED_D5.0mm
DBI1: 19X7_INPUTS; DSUB-37_Female_Vertical_P2.77x2.84mm_MountingHoles
DBO1: 19X6_OUTPUTS; DSUB-37_Female_Vertical_P2.77x2.84mm_MountingHoles
E1: Chassis; MountingHole_4.5mm_Pad
G1, G2, G3: G; XY2500V-C(5.08)-2P
G4, G5: XY2500R-C(5.08)-2P
GA1, GA2, GA3: GA; XY2500V-C(5.08)-2P
H1, H2, H3, H4, H5, H6: MountingHole; MountingHole_4.5mm
IN1, IN2, IN3, IN4, IN5, IN6, IN7, IN8: IN; XY2500V-C(5.08)-3P
IX1, IX2, IX3: XY2500R-C(5.08)-3P
IX4, IX5, IX6, IX7, IX8, IX9: XY2500R-C(5.08)-2P
JP1: PWR_SELECT; PinSocket_2x03_P2.54mm_Vertical
JP2: GND_BRIGDE; PinSocket_2x03_P2.54mm_Vertical
OUT1, OUT2, OUT3, OUT4, OUT5, OUT6: OUT; XY2500V-C(5.08)-2P
OUTX1, OUTX2, OUTX3: XY2500R-C(5.08)-2P
R1, R2, R3: R; R_0805_2012Metric
RJ1: SSERIAL; MTJ-88FX1
S1: S1; XY2500V-C(5.08)-2P
S2: S2; XY2500V-C(5.08)-2P
S3: S3; XY2500V-C(5.08)-2P
SS1: SS1; XY2500V-C(5.08)-4P
SS2: SS2; XY2500V-C(5.08)-4P
U1, U3: XY2500R-C(5.08)-2P
U2: XY2500R-C(5.08)-3P
V1, V2, V3: V; XY2500V-C(5.08)-2P
V4, V5: XY2500R-C(5.08)-2P
VA1, VA2, VA3: VA; XY2500V-C(5.08)-2P

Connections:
/19X6_HANDWHEEL_X: DBO1.1, OUTX1.1
/19X6_HANDWHEEL_Y: DBO1.3, OUTX2.1
/19X6_HANDWHEEL_Z: DBO1.2, OUTX3.1
/19X7_200_HIGH: DBI1.4, IN4.1
/19X7_HANDWHEEL_X: DBI1.1, IN2.2
/19X7_HANDWHEEL_Y: DBI1.3, IN3.1
/19X7_HANDWHEEL_Z: DBI1.2, IN3.2
/19X7_LUBRICANT: DBI1.7, IN5.2
/19X7_MAIN_DRIVE_OFF: DBI1.5, IN4.2
/19X7_NOT_SPINDLE_FEED: DBI1.6, IN5.1
/200_NORMAL: OUT2.1, OUT3.1, OUT4.1, OUT5.1, OUT6.1, OUTX1.2, OUTX2.2, OUTX3.2, U2.2
/202_24V: R3.1, U3.1, VA1.1, VA1.2, VA2.1, VA2.2, VA3.1, VA3.2
/204_24V/a: JP1.5, JP1.6, R2.1, U2.1
/CENTRAL_LUBRICATION: DBO1.8, OUT6.2
/COOLANT_PUMP: DBO1.6, OUT4.2
/E101: A1.1, S1.1
/E102: A1.2, S1.2
/E201: A1.3, S3.1
/E202: A1.4, S3.2
/E301: A1.5, S2.1
/E302: A1.9, S2.2
/EXT_ESTOP: IN6.1, IX4.1
/EXT_PWR: JP1.1, JP1.2, R1.1, U1.1
/IN12: IN7.1, IX6.1
/IN13: IN7.2, IX7.1
/IN14: IN8.1, IX8.1
/IN15: IN8.2, IX9.1
/LIMIT_X: IN1.1, IX1.2
/LIMIT_Ζ: IN2.1, IX3.2
/LIMIT_Υ: IN1.2, IX2.2
/PON_SWITCH: IN6.2, IX5.1
/SPINDLE_CCW: DBO1.5, OUT3.2
/SPINDLE_CW: DBO1.4, OUT2.2
/SS_5VP: RJ1.7, RJ1.8, SS2.3, SS2.4
/SS_RX+: RJ1.6, SS1.3
/SS_RX-: RJ1.3, SS1.4
/SS_TX+: RJ1.2, SS2.1
/SS_TX-: RJ1.1, SS2.2
/TOOL_RELEASE: DBO1.7, OUT5.2
//ESTOP: DBO1.34, OUT1.2
Earth: A1.0 (PAD), DBI1.0 (PAD), DBO1.0 (PAD), E1.1
GND: D1.1 (K), D2.1 (K), G1.1, G1.2, G2.1, G2.2, G3.1, G3.2, G4.1, G4.2, G5.1, G5.2, IN1.3, IN2.3, IN3.3, IN4.3, IN5.3, IN6.3, IN7.3, IN8.3, IX1.1, IX2.1, IX3.1, JP2.1, JP2.3, JP2.5, RJ1.4, RJ1.5, SS1.1, SS1.2, U1.2, U2.3
GNDA: D3.1 (K), GA1.1, GA1.2, GA2.1, GA2.2, GA3.1, GA3.2, JP2.2, JP2.4, JP2.6, U3.2
unnamed: D1.2 (A), R1.2
unnamed: D2.2 (A), R2.2
unnamed: D3.2 (A), R3.2
VDC: IX1.3, IX2.3, IX3.3, IX4.2, IX5.2, IX6.2, IX7.2, IX8.2, IX9.2, JP1.3, JP1.4, OUT1.1, V1.1, V1.2, V2.1, V2.2, V3.1, V3.2, V4.1, V4.2, V5.1, V5.2

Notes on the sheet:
IN12
ANALOG_Y1
ANALOG_Z1
IN7
IN4
204
IN15
IN2
201
IN13
ANALOG_Z2
ANALOG_X1
IN8
IN14
202
ANALOG_Y2
IN3
IN5
IN1
IN6
IN11
IN9
IN0
203
ANALOG_X2
IN10
200

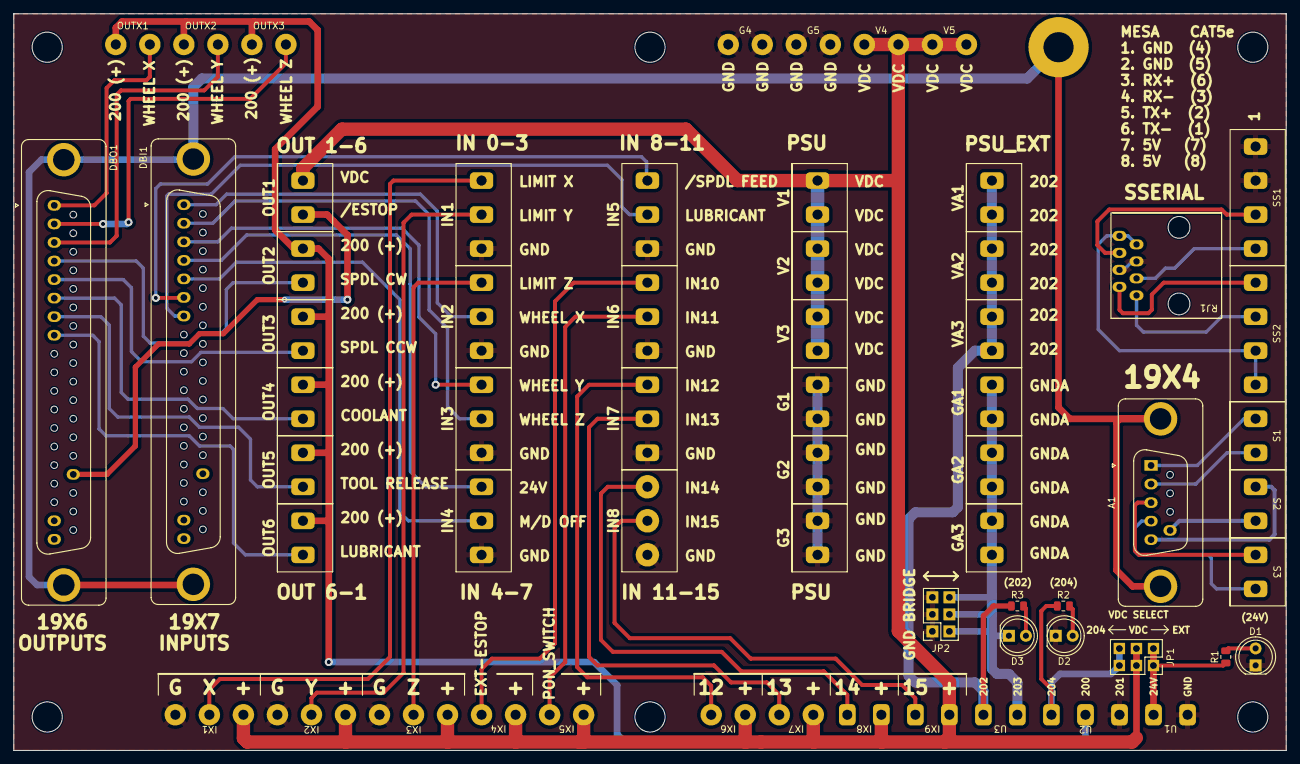
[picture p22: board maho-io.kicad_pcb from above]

Board: 2 copper layers, 190.0 x 110.0 mm, 69 parts (0 on the bottom side), 47 nets.

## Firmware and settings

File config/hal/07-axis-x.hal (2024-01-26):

setp pid.x.Pgain [JOINT_0](P)
setp pid.x.Igain [JOINT_0](I)
setp pid.x.Dgain [JOINT_0](D)
setp pid.x.bias [JOINT_0](BIAS)
setp pid.x.FF0 [JOINT_0](FF0)
setp pid.x.FF1 [JOINT_0](FF1)
setp pid.x.FF2 [JOINT_0](FF2)
setp pid.x.deadband [JOINT_0](DEADBAND)
setp pid.x.maxoutput [JOINT_0](MAX_OUTPUT)
# setp pid.x.maxerror [JOINT_0](MAX_ERROR)
setp pid.x.error-previous-target true

# PWM pin0
setp hm2_7i97.0.pwmgen.00.output-type 1        
# offset mode so 50% = 0
setp hm2_7i97.0.pwmgen.00.offset-mode 1
setp hm2_7i97.0.pwmgen.00.scale [JOINT_0](OUTPUT_SCALE)

setp hm2_7i97.0.encoder.00.counter-mode 0
setp hm2_7i97.0.encoder.00.filter 1
setp hm2_7i97.0.encoder.00.index-invert 0
setp hm2_7i97.0.encoder.00.index-mask 0
setp hm2_7i97.0.encoder.00.index-mask-invert 0
setp hm2_7i97.0.encoder.00.scale  [JOINT_0](ENCODER_SCALE)

net joint.net.0.enable  => pid.x.enable
net joint.net.0.enable  => joint.0.amp-enable-out
net joint.net.0.enable  => hm2_7i97.0.pwmgen.00.enable

net joint.net.0.pos-cmd => pid.x.command
net joint.net.0.pos-cmd => joint.0.motor-pos-cmd

net joint.net.0.pos-fb => pid.x.feedback
net joint.net.0.pos-fb => joint.0.motor-pos-fb
net joint.net.0.pos-fb => hm2_7i97.0.encoder.00.position

net joint.net.0.output => pid.x.output
net joint.net.0.output => hm2_7i97.0.pwmgen.00.value

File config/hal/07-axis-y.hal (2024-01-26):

setp pid.y.Pgain [JOINT_1](P)
setp pid.y.Igain [JOINT_1](I)
setp pid.y.Dgain [JOINT_1](D)
setp pid.y.bias [JOINT_1](BIAS)
setp pid.y.FF0 [JOINT_1](FF0)
setp pid.y.FF1 [JOINT_1](FF1)
setp pid.y.FF2 [JOINT_1](FF2)
setp pid.y.deadband [JOINT_1](DEADBAND)
setp pid.y.maxoutput [JOINT_1](MAX_OUTPUT)
# setp pid.y.maxerror [JOINT_1](MAX_ERROR)
setp pid.y.error-previous-target true

# PWM pin0
setp hm2_7i97.0.pwmgen.01.output-type 1        
# offset mode so 50% = 0
setp hm2_7i97.0.pwmgen.01.offset-mode 1
setp hm2_7i97.0.pwmgen.01.scale [JOINT_1](OUTPUT_SCALE)

setp hm2_7i97.0.encoder.01.counter-mode 0
setp hm2_7i97.0.encoder.01.filter 1
setp hm2_7i97.0.encoder.01.index-invert 0
setp hm2_7i97.0.encoder.01.index-mask 0
setp hm2_7i97.0.encoder.01.index-mask-invert 0
setp hm2_7i97.0.encoder.01.scale  [JOINT_1](ENCODER_SCALE)

net joint.net.1.enable  => pid.y.enable
net joint.net.1.enable  => joint.1.amp-enable-out
net joint.net.1.enable  => hm2_7i97.0.pwmgen.01.enable

net joint.net.1.pos-cmd => pid.y.command
net joint.net.1.pos-cmd => joint.1.motor-pos-cmd

net joint.net.1.pos-fb => pid.y.feedback
net joint.net.1.pos-fb => joint.1.motor-pos-fb
net joint.net.1.pos-fb => hm2_7i97.0.encoder.01.position

net joint.net.1.output => pid.y.output
net joint.net.1.output => hm2_7i97.0.pwmgen.01.value

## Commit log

2023-04-16 maho-io release for fab
    [maho-io-B_Cu.gbr, maho-io-B_Mask.gbr, maho-io-B_Paste.gbr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]
2023-04-16 maho-io screenshots
    [maho-io-B_Cu.gbr, maho-io-B_Mask.gbr, maho-io-B_Paste.gbr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]
2023-04-17 maho-io component and english manual
    [ETSOP.kicad_sch, Encoders.kicad_sch, MAHO_Inputs.kicad_sch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]
2023-04-25 updates analog
    [LinearEncoders.kicad_sch, maho-io.kicad_sch, retrofit.kicad_sch]
2023-05-07 updates with new board
    [2-inputs.hal, 3-estop.hal, 3-limits.hal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]
2024-01-23 by the book
    [1-base.hal, 11-sserial.hal, 12-buttons.hal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]
